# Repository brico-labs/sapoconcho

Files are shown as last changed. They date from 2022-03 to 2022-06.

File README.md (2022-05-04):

# [sapoconcho.bricolabs.cc](http://sapoconcho.bricolabs.cc)

Sapoconcho es un robot open-source educativo con que que introducirse en el mundo de la robótica y la programación. 
 
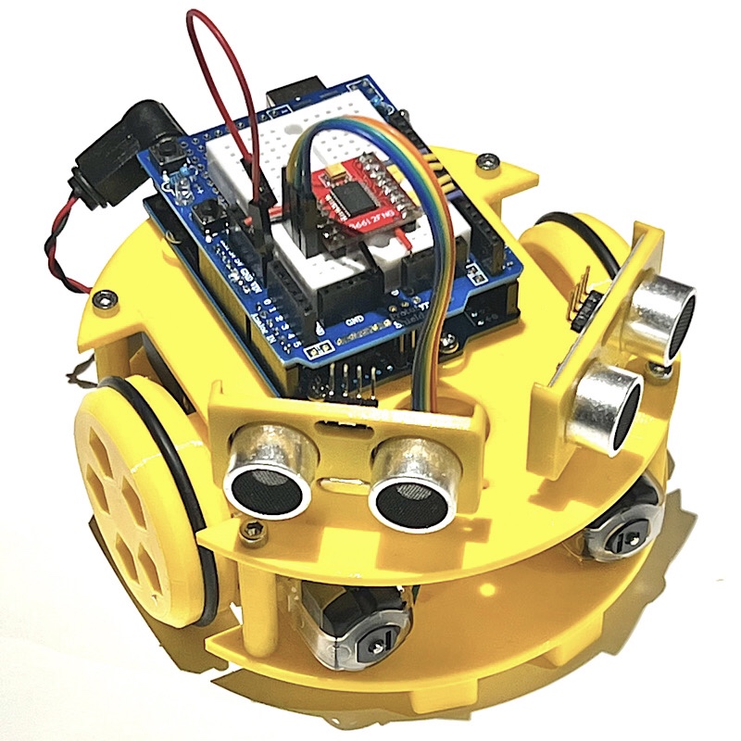
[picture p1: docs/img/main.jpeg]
Sapoconcho


Está ideado con el objetivo de ser lo más accesible posible:
- Componentes comunes, fáciles de encontrar y económicos.
- Diseño sencillo para imprimir y montar.
- Modular y extensible.

En este repositorio encontrarás:
- `3d_models` Los modelos 3D necesarios para crear un kit.
- `arduino` Ejemplos de código de programación del robot.
- `docs` Fuentes de la documentación que genera el sitio [sapoconcho.bricolabs.cc](https://sapoconcho.bricolabs.cc)

Revisa nuestro [CONTRIBUTING.md](CONTRIBUTING.md) si quieres modificar este repositorio o el sitio web.

Este proyecto antes estaba alojado en: 

- https://bricolabs.cc/wiki/proyectos/montaje_sapoconcho_xl
- https://bricolabs.cc/wiki/proyectos/sapoconcho
- https://github.com/felixstdp/sapoconcho

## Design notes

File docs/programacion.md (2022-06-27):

# Programación de Sapoconcho

Ahora que ya tienes tu Sapoconcho montado.. ¡vamos a programarlo!

Lo primero que necesitas es [Arduino IDE](https://www.arduino.cc/en/software), el programa que te permitirá escribir el código en el robot. Una vez instalado conecta el Arduino al ordenador usando el cable USB de tu kit y abre Arduino IDE.

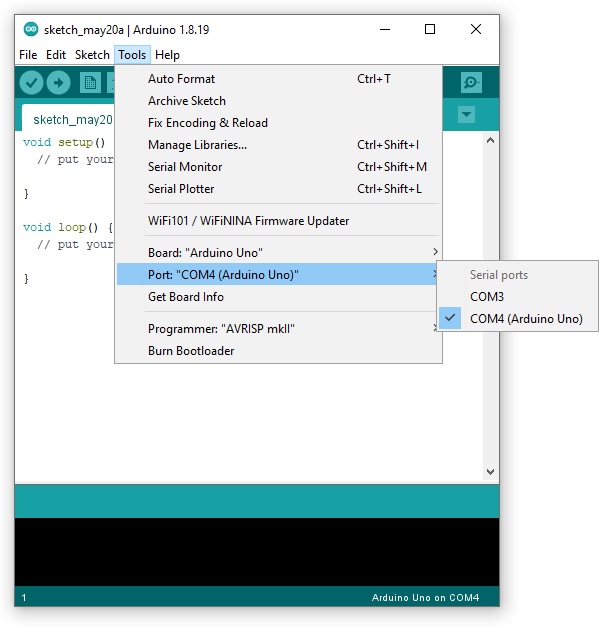
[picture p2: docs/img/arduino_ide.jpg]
Arduino IDE


En el menú *tools* selecciona:

- Board: Arduino Uno
- Puerto: el puerto USB en el que tienes conectado el Arduino.

## Programando en Arduino
Programar en Arduino es muy sencillo, tenemos dos funciones en las que escribir nuestro código:

- Setup: el robot hará lo que escribas aquí cuando se encienda.
- Loop: el robot hará esto continuamente una vez finalice el setup.

```c
void setup() {

}

void loop(){

}
```

!!! Note "Truco"

    Lo que escribas después de una doble barra "//" no se ejecutará, puedes usarlo para poner anotaciones en el código.

## Función de movimiento
Para decirle al robot que se mueva vamos a usar una función *drive* que os damos a continuación (copia y pégala al final de tu código):

```c
// Drive permite manejar los motores
// Izquierda y derecha admite valores de -100 a 100
// Tiempo en milisegundos
void drive(int izquierda, int derecha, int tiempo) 
{
  //Arduino UNO y driver TB6612/DRV8833
  const int AIN2 = 9; // PWMA
  const int AIN1 = 8;
  const int BIN1 = 7;
  const int BIN2 = 6; // PWMB

  pinMode(AIN1,OUTPUT);
  pinMode(AIN2,OUTPUT);
  pinMode(BIN1,OUTPUT);
  pinMode(BIN2,OUTPUT);

  izquierda=map(constrain(izquierda,-100,100),-100,100,-255,255);
  derecha=map(constrain(derecha,-100,100),-100,100,-255,255);

  digitalWrite(AIN1, izquierda<0);
  analogWrite(AIN2, izquierda + 255 * (izquierda < 0));
  digitalWrite(BIN1, derecha < 0);
  analogWrite(BIN2, derecha + 255 * (derecha < 0));

  delay(tiempo);
}
```

Esta función nos permite decirle al robot la velocidad de la rueda izquierda, rueda derecha y un tiempo. La velocidad de cada rueda admite valores de -100 a 100. El tiempo debemos indicarlo en milisegundos (1 segundo son 1000).

Ahora debemos llamar a esta función, para ello copia y pegar la siguiente linea dentro del *loop* de tu programa:
```c
drive(50,50,1000);
```

Para enviar el código al robot debes pulsar el botón *upload* upload.

Verás una barra de progreso y en unos pocos segundos ¡tu robot habrá recibido su primer código!

Ahora desconecta el cable USB del Sapoconcho, ponle la alimentación de las pilas y comprueba que avanza hacia delante.

??? Note "¿Sapoconcho avanza en linea recta?"

    Probablemente no.. esto se debe a que no existen dos motores exactamente iguales en el mundo y aunque les ordenemos ir a la misma velocidad no podrán. Intenta ajustar los valores *izquierda* y *derecha* para que tu sapoconcho avance recto.

**Movimientos de prueba**

Habrás notado que aunque le hemos puesto que avance un segundo Sapoconcho no para. Prueba a introducir una segunda instrucción a continuación de la anterior para indicar a sapoconcho que pare:

```c
drive(0,0,1000);
```

Si le envías este programa a Sapoconcho ahora verás que camina y para continuamente, ¡Esta es la mágia de la función *loop*! 

??? note "¿Se te ocurre como hacer que pare definitivamente?"

    ¡Exacto! En lugar de poner el código en el *loop* muévelo al *setup*, de esta forma sólo seguirá tus instrucciones una vez.

Ahora puedes probar a jugar con las distintas opciones que nos da la función *drive* y encadenarlas para conseguir una secuencia de movimientos:

- Movimiento hacia adelante: izquierda y derecha con valores positivos.
- Movimiento hacia atrás: izquierda y derecha con valores negativos.
- Giro en redondo: izquierda positivo, derecha negativo o viceversa.
- Giro en avance: valor de una rueda mayor que el de la otra.
- Parar: valores de izquierda y derecha en 0.

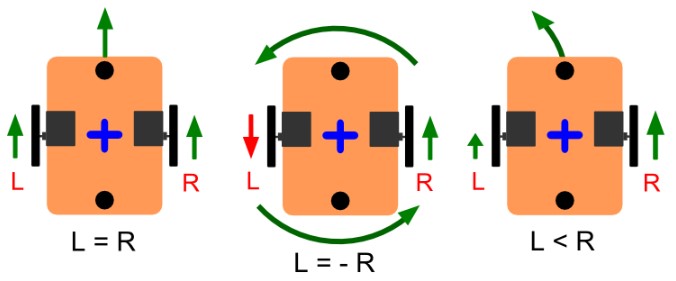
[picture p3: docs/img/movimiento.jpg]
Movimiento


??? note "¿Eres capaz de hacer un giro de 90 grados?"

    Para hacerlo deberás ajustar el tiempo que el robot está girando en redondo.

    Si lo consigues, intenta hacer un giro de 180 grados.

??? note "Intenta que el robot dibuje la forma de un cuadrado."

    Deberás concatenar avances y giros en redondo hacia un lado. Al estar en un bucle infinito solo necesitas dos instrucciones para conseguirlo.

    Si lo consigues, prueba con otras formas geométricas.

??? note "¿Saponconcho podrá moverse como una serpiente?"

    Concatenando varios giros en avance puedes conseguir que Sapoconcho se mueva en eses.

    Prueba a ponerle obstáculos e intenta evitarlos serpenteando.

## Sensores de ultrasonidos

Los sensores del ultrasonidos permiten a Sapoconcho medir la distancia a los objetos que tiene delante.

!!! info inline end "Sensor de ultrasonidos"

    El sensor HC-SR04 tiene cuatro pines: alimentación (VCC), trigger, echo y masa (GND), Trigger y echo los hemos unido con una soldadura para ahorrarnos un cable, aunque tenemos que advertir que es posible que modelos de algunos fabricantes no permitan esto, y al hacerlo no funcionen. 

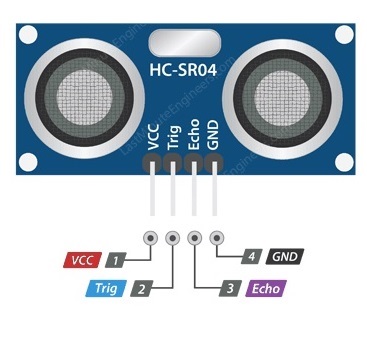
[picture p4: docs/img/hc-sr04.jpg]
hc-sr04


Los sensores tienen casi siempre dos pines de alimentación y uno o más pines de datos. La protoshield tiene en un lateral dos líneas para conectar la alimentación a positivo (5V) y negativo (GND).

Cablearemos con cables Dupont hembra-macho del sensor a la protoshield.

- VCC a uno de los conectores de 5V.
- GND a uno de los de masa.
- Trig o Echo al pin digital 2 del Arduino.

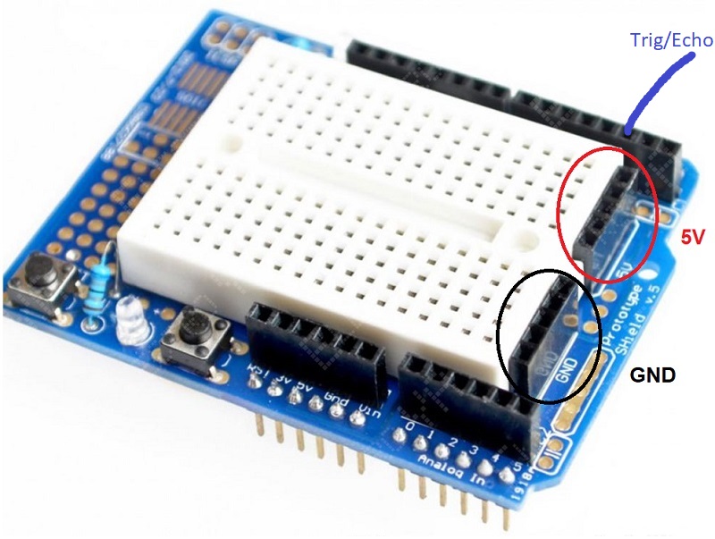
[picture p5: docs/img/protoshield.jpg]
Protoboard


El montaje del soporte a la placa superior es sencillo, con un tornillo M3x10 y una tuerca. La placa tiene tres orificios, usaremos el central para montar un único sensor o los laterales para montar dos.

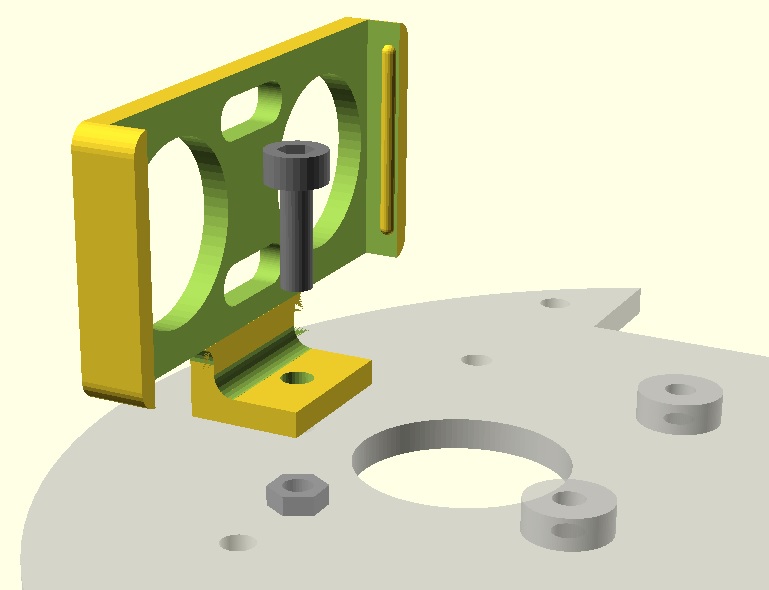
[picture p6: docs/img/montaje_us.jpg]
Montaje ultrasonidos


Para leer la distancia que mide el sensor usaremos una nueva función, que de nuevo copiaremos y pegaremos al final de nuestro programa.

```c
unsigned long sonar(int pin)
{
  double calibracion = 0.017; // Calibración del sensor
  pinMode(pin, OUTPUT);
  digitalWrite(pin,LOW); // Envía un pulso ultrasónico
  delayMicroseconds(5);
  digitalWrite(pin, HIGH);
  delayMicroseconds(10);
  pinMode(pin, INPUT);
  unsigned long tiempo=pulseIn(pin, HIGH); // Espera a recibir la respuesta
  unsigned long distancia= int(calibracion*tiempo); // Calcula la distancia
  return distancia;
}
```

Para usarla debemos llamarla pasándole el pin al que hemos conectado el sensor, en este caso el 2. Esta función nos devuelve un valor que guardaremos en una variable *distancia*.

```c
long int distancia = sonar(2);
```

El siguiente código permite leer el sensor y mostrar el resultado en el ordenador para poder comprobar que funciona y calibrarlo. Sapoconcho nos enviará los datos a través del cable USB.

??? Código
    ```c
    void setup()
    {
      Serial.begin(9600);
    }

    void loop()
    {
      unsigned long distancia = sonar(2); // invocamos a función de medir distancia
      Serial.print("Distancia: "); // Enviamos los valores a la consola
      Serial.print(distancia);
      Serial.println(" cm");
    }

    unsigned long sonar(int pin)
    {
      double calibracion = 0.017; // Calibración del sensor
      pinMode(pin, OUTPUT);
      digitalWrite(pin,LOW); // Envía un pulso ultrasónico
      delayMicroseconds(5);
      digitalWrite(pin, HIGH);
      delayMicroseconds(10);
      pinMode(pin, INPUT);
      unsigned long tiempo=pulseIn(pin, HIGH); // Espera a recibir la respuesta
      unsigned long distancia= int(calibracion*tiempo); // Calcula la distancia
      return distancia;
    }
    ```

En el ordenador deberemos abrir el monitor serial que está en la barra superior en el margen derecho serial.

!!! Note ""

    Al igual que con los motores, cada sensor es diferente y tendremos que calibrar el nuestro para que mida correctamente los centímetros. Puedes probar a ajustar la variable calibracion dentro de la función sonar para que los valores que te muestra sean más realistas.

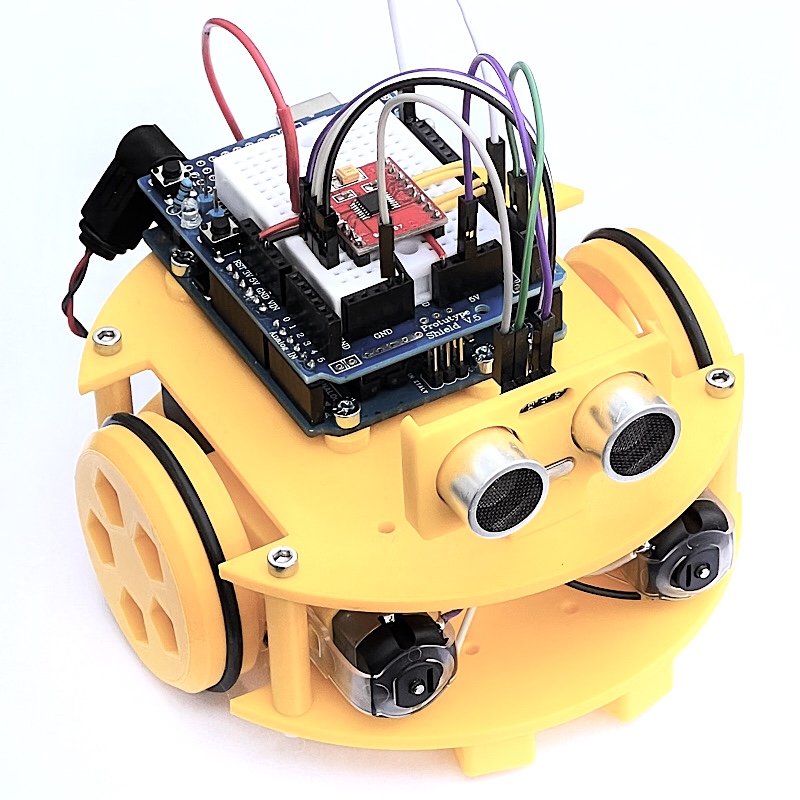
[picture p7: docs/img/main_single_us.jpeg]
Sapoconcho 1 us


**Mantener la distancia** 

Para utilizar el sensor combinado con el movimiento en Sapoconcho necesitaremos utilizar la instrucción *if - else*. En el siguiente programa comprobamos la distancia, si el obstáculo está lejos le decimos al robot que avance, si está cerca que retroceda.

??? Código
    ```c
    void setup() {

    }

    void loop() {
      long int distancia = sonar(2);
      if (distancia<10){
        drive(-75,-75,50);
      }
      else {
        drive(75,75,50);
      }
    }

    void drive(int izquierda, int derecha, int tiempo) 
    {
      //Arduino UNO y driver TB6612/DRV8833
      const int AIN2 = 9; // PWMA
      const int AIN1 = 8;
      const int BIN1 = 7;
      const int BIN2 = 6; // PWMB

      pinMode(AIN1,OUTPUT);
      pinMode(AIN2,OUTPUT);
      pinMode(BIN1,OUTPUT);
      pinMode(BIN2,OUTPUT);

      izquierda=map(constrain(izquierda,-100,100),-100,100,-255,255);
      derecha=map(constrain(derecha,-100,100),-100,100,-255,255);

      digitalWrite(AIN1, izquierda<0);
      analogWrite(AIN2, izquierda + 255 * (izquierda < 0));
      digitalWrite(BIN1, derecha < 0);
      analogWrite(BIN2, derecha + 255 * (derecha < 0));

      delay(tiempo);
    }

    unsigned long sonar(int pin)
    {
      double calibracion = 0.017; // Calibración del sensor
      pinMode(pin, OUTPUT);
      digitalWrite(pin,LOW); // Envía un pulso ultrasónico
      delayMicroseconds(5);
      digitalWrite(pin, HIGH);
      delayMicroseconds(10);
      pinMode(pin, INPUT);
      unsigned long tiempo=pulseIn(pin, HIGH); // Espera a recibir la respuesta
      unsigned long distancia= int(calibracion*tiempo); // Calcula la distancia
      return distancia;
    }
    ```

Esto evitará que el robot choque con una pared hacia la que va de frente, ademássi en lugar de una pared ponemos la mano, conseguiremos manejar 'a distancia' nuestro robot.

!!! Note ""

    Como diversión si estamos trabajando en grupo podemos poner todos los robots en fila y encenderlos a la vez a ver qué pasa.

**Evitar obstáculos**  

Si a nuestro robot le ponemos dos sensores de distancia podemos ver por donde está el obstáculo más cercano y girar hacia el lado contrario evitándolo.

??? Código
    ```c
    void setup() {
    }

    void loop() {
      long int izquierda = sonar(2);
      long int derecha = sonar(3);
      long int distancia = min(izquierda, derecha);
      if (distancia<10){
        if (izquierda<derecha){
          drive(75,-75,100);
        }
        else{
          drive(-75,75,100);
        }
      }
      else{
        drive(75,75,50);
      }
    }

    void drive(int izquierda, int derecha, int tiempo) 
    {
      //Arduino UNO y driver TB6612/DRV8833
      const int AIN2 = 9; // PWMA
      const int AIN1 = 8;
      const int BIN1 = 7;
      const int BIN2 = 6; // PWMB

      pinMode(AIN1,OUTPUT);
      pinMode(AIN2,OUTPUT);
      pinMode(BIN1,OUTPUT);
      pinMode(BIN2,OUTPUT);

      izquierda=map(constrain(izquierda,-100,100),-100,100,-255,255);
      derecha=map(constrain(derecha,-100,100),-100,100,-255,255);

      digitalWrite(AIN1, izquierda<0);
      analogWrite(AIN2, izquierda + 255 * (izquierda < 0));
      digitalWrite(BIN1, derecha < 0);
      analogWrite(BIN2, derecha + 255 * (derecha < 0));

      delay(tiempo);
    }

    unsigned long sonar(int pin)
    {
      double calibracion = 0.017; // Calibración del sensor
      pinMode(pin, OUTPUT);
      digitalWrite(pin,LOW); // Envía un pulso ultrasónico
      delayMicroseconds(5);
      digitalWrite(pin, HIGH);
      delayMicroseconds(10);
      pinMode(pin, INPUT);
      unsigned long tiempo=pulseIn(pin, HIGH); // Espera a recibir la respuesta
      unsigned long distancia= int(calibracion*tiempo); // Calcula la distancia
      return distancia;
    }
    ```

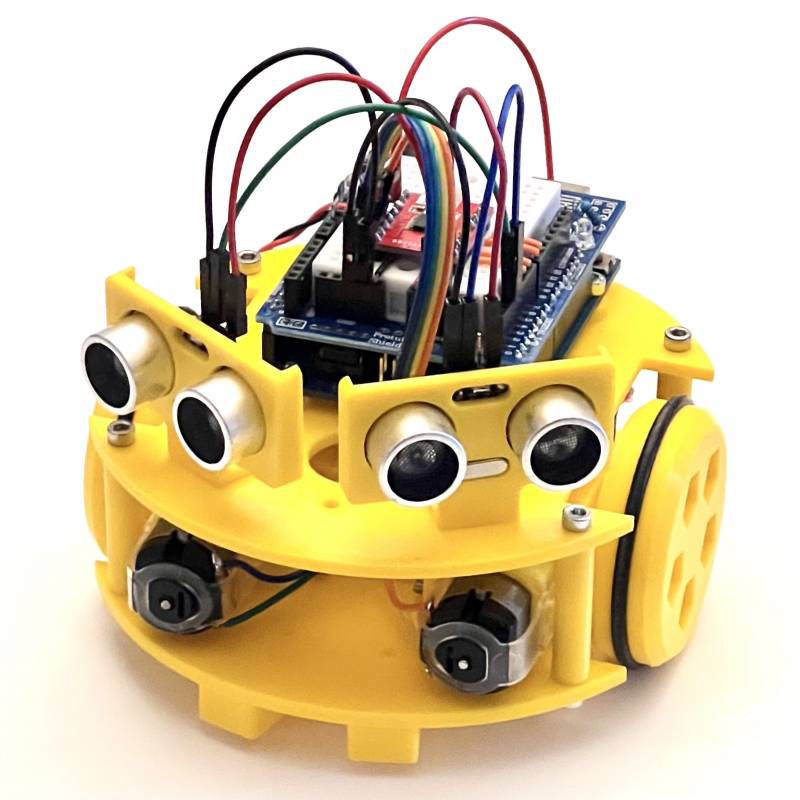
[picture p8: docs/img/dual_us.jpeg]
Sapoconcho 2 us


!!! Note ""

    Esto también es posible hacerlo con un solo sensor, pero tendrás que parar el robot y girarlo para medir en que dirección está el terreno más despejado ¿Eres capaz de hacerlo?

## Sensores de líneas

Los sensores infrarrojos de líneas, tanto con salida analógica como digital utilizan tres pines: alimentación (VCC), masa (GND) y señal. Debes revisar tu sensor, según el fabricante los sensores podrían estar en otro orden, no tiene por qué coincidir con la foto.

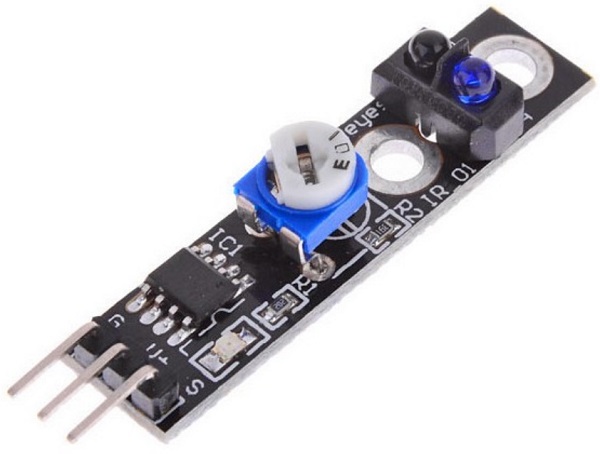
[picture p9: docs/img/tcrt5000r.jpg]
tcrt5000r


Utilizaremos sensores basados en reflexión TCRT5000 con regulador (importante) que se montarán en el chasis inferior y se cablean a 5v, GND y dos entradas analógicas entre A0 y A5 (con cables Dupont H-M de 20cm).

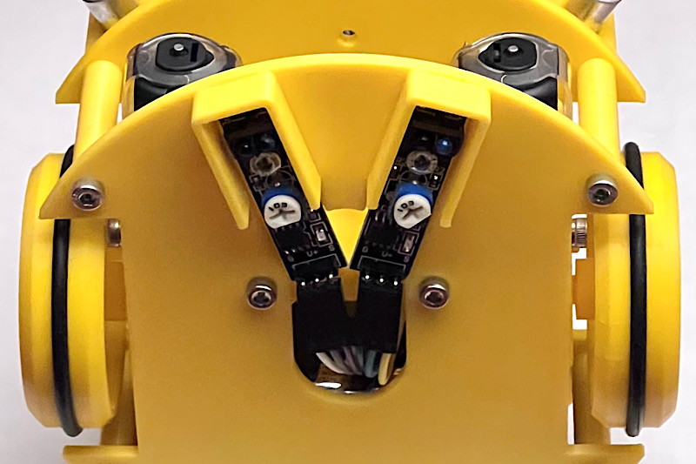
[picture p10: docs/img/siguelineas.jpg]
Siguelineas


**Seguir una línea**

Para leer los sensores no necesitamos una función extra, Arduino puede hacerlo con su propia función analogRead(pin). El siguiente código lee los dos sensores y si uno de ellos está sobre la línea negra gira hacia el otro lado para evitarla (necesita la función drive).

```c
void setup() {
}

void loop()
{
  if (analogRead(A0)<500){
    drive(-75,75,100);
  }
  if (analogRead(A1)<500) {
    drive(75,-75,100);
  } 
  drive(75,75,100);
}
```

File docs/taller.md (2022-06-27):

# Preparar un taller de Sapoconcho

Sapoconcho fue concebido principalmente para impartir talleres de robótica. El público principal para el que está pensado es para niños de entre 11 y 18 años o formadores que posteriormente utilizarán Sapoconcho en sus clases. Es muy habitual y recomendable que si los niños son pequeños (11-14 años) hagan el taller acompañados por un adulto.

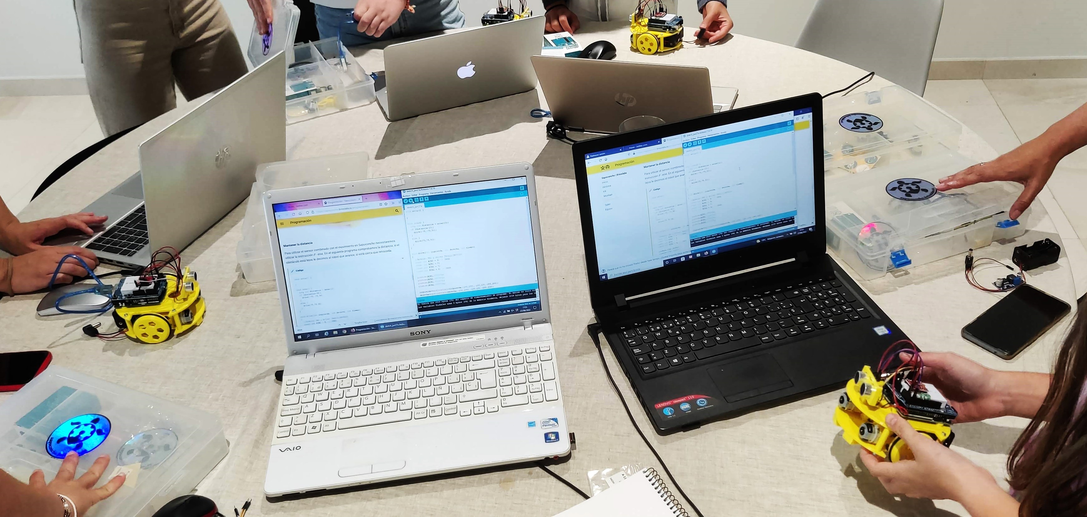
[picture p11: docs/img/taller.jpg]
taller


## Duración del taller
Basándonos en experiencias anteriores podemos indicar las siguientes duraciones:

- Montaje: 60 minutos
- Programación movimiento: 45 minutos
- Programación ultrasonidos: 45 minutos
- Programación siguelineas: 45 minutos

Es posible alargar el taller o dividirlo en dos sesiones si se incluye la parte de preparado de los kits. Para esta parte la edad recomendada debería ser un poco mayor ya que requiere soldar con estañador.

## Preparativos previos

### Preparando los kits

Las siguientes indicaciones pueden ahorrarnos problemas durante el taller:

- Preparar al menos un 1 kit extra por cada 10 por si faltan o fallan piezas en alguno.
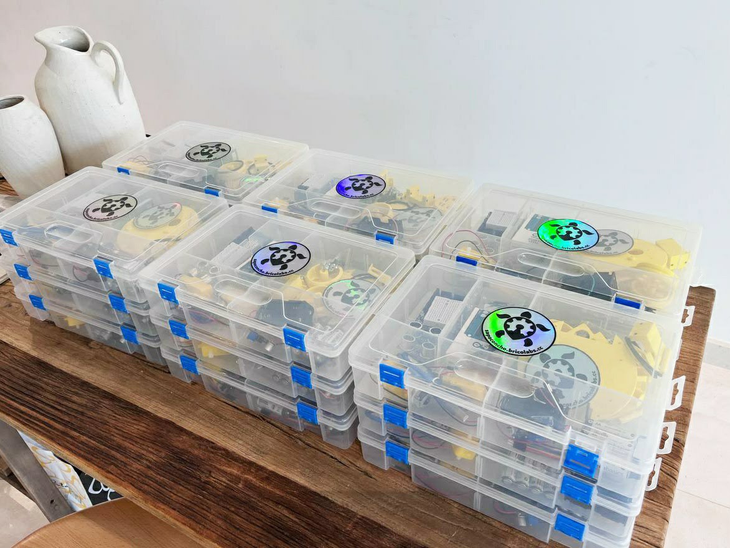
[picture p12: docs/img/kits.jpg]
kits

- Revisar los diámetros de los agujeros en las piezas impresas, especialmente los del eje de los motores que deben entrar justos.
- Soldar los pines del driver de motores.
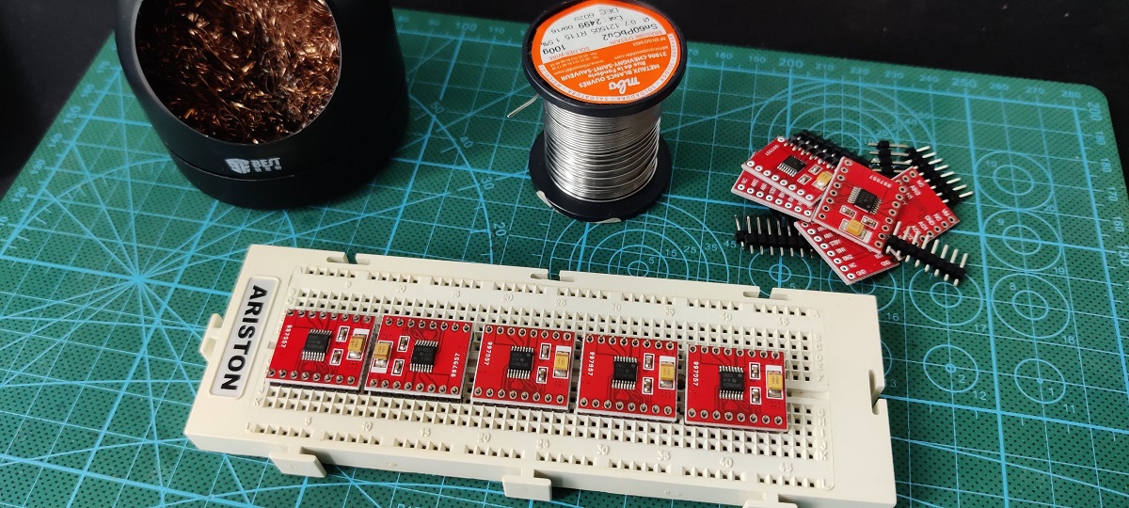
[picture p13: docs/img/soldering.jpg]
soldering

- Cortar y pelar los cables para breadboard a medida.
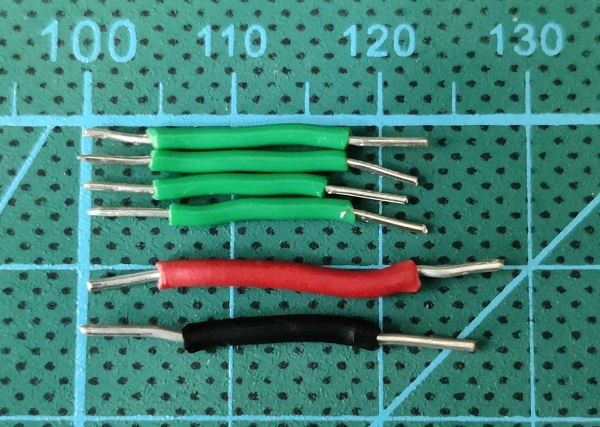
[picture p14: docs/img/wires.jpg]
wires

- Soldar cables al step-up y al conector de alimentación.
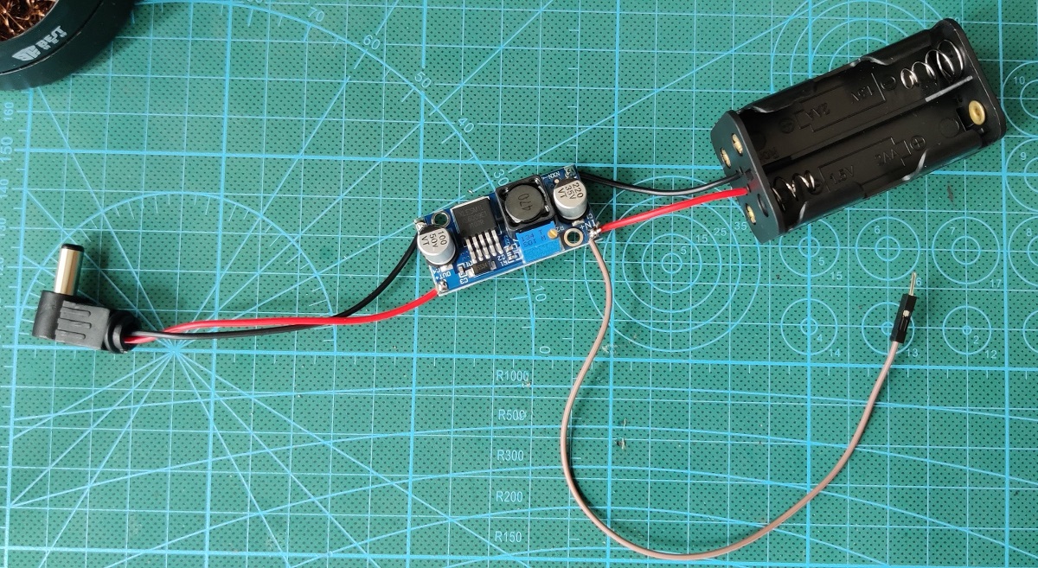
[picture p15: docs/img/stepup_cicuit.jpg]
stepup_cicuit

- Regular el voltaje del step-up.
- Soldar los dos pines centrales del sensor de ultrasonidos.

### Preparativos de los participantes
Es recomendable que los participantes traigan Arduino IDE instalado en sus portátiles de forma que evitemos problemas con la descarga o instalación durante el taller.

## Durante el taller

Es recomendable tener a mano los siguientes materiales y herramientas por si fuesen necesarias:  

- Estación de soldadura (estañador, estaño y demás útiles)
- Destornillador eléctrico con punta hexagonal
- Cable para breadboard
- Alicates de corte
- Pelacables
- Multímetro
- Lima y broca de 3mm (por si los diámetros del eje de las ruedas fuesen pequeños)
- Loctite (por si los diámetros del eje de las ruedas son demasiado holgados)
- Cinta de doble cara
- Bridas
- Instalador de Arduino IDE en un pen-drive

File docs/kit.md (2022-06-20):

# Un Kit Sapoconcho

Un kit de Sapoconcho es un paquete con todas las piezas necesarias para montar un Sapoconcho. Para hacerte uno necesitarás una serie de materiales que detallaremos a continuación:

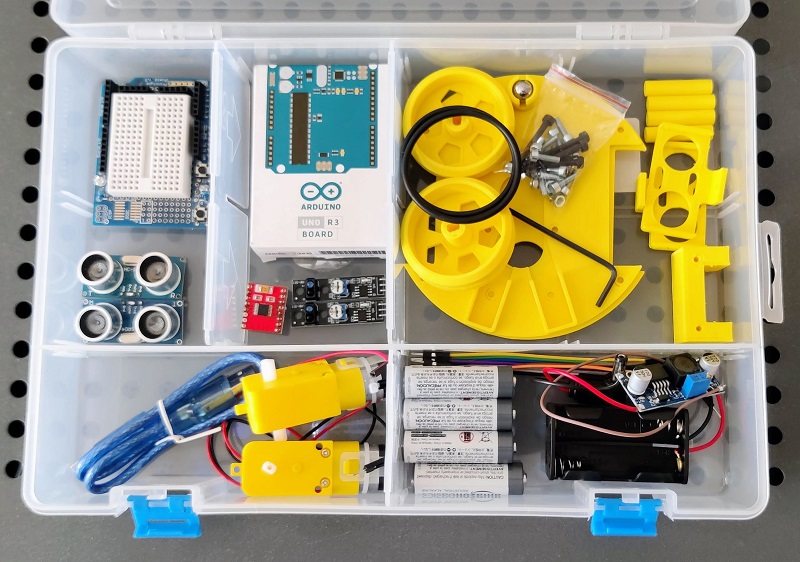
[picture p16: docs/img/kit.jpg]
kit


## Piezas imprimibles
El chasis de Sapoconcho consta de las siguientes piezas:

- Bases superior e inferior.
- Soporte de motores (1 unidad).
- Pilares de unión (o separación) de las dos bases (4 unidades). Pueden usarse en su lugar separadores de circuitos de 30mm.
- Ruedas (2 unidades).
- Soporte de sensores de ultrasonidos (1 ó 2 unidades).

En una impresora típica de 200x200mm se pueden imprimir todas las piezas en dos tandas.

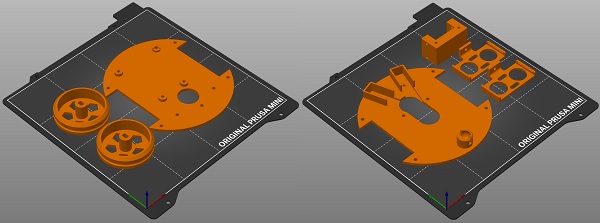
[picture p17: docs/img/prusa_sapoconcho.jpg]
Impresion3D


Todas las piezas están en [este repositorio de Github](https://github.com/brico-labs/sapoconcho/tree/main/3d_models). Ahí puedes encontrar los archivos originales de OpenSCAD para modificarlos a tu gusto o los STL para imprimir directamente.

## Listado de materiales (BOM)

- Arduino UNO o compatible.
- Protoshield para Arduino UNO.
- Driver de motores TB6612 o DRV8833.
- Dos motores amarillos. Sabemos que es un término muy genérico, pero si estás metido un poco en el mundo maker/DIY o haces una búsqueda rápida en tu plataforma favorita verás a qué nos referimos. Es un tipo de motor de corriente continua muy usado en todo tipo de proyectos y kits, muy fácil de conseguir y muy económico. No necesitamos las ruedas que traen a veces.
- Gomas de fontanería para las ruedas (2ud). Medida 45×3 mm.
- Bola de acero de 10 mm.
- Sensores ultrasónicos HC-SR04 (1 ó 2 ud).
- Sensores de líneas por infrarrojos (2 ud).
- Portapilas para montar 4 pilas AA (dos encima y dos debajo).
- Elevador de tensión DC-DC (step-up, con los integrados LM2587/XL6009).
- Clavija de alimentación para Arduino UNO (5.5×2.1 mm).
- Tornillos M3 (12 ud M3x10, 4 ud M3x30, 4d M3x6).
- Tuercas M3 (4 ud).
- Cables Dupont M-H de 20mm y de 10mm.
- Cable USB-A a USB-B
- Cables de tres colores (rojo, negro y otro) para breadboard.

Por si os es de utilidad, os dejamos una [lista de la compra en Amazon](https://www.amazon.es/hz/wishlist/ls/9FKST3X6WCM?viewType=list).

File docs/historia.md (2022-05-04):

# Historia

!!! Note ""

    Yet Another Training Robot.

## El origen

Sabemos que lo que hacemos no es ninguna novedad. Este tipo de robots se puede encontrar en modelos comerciales y en muchos tutoriales a lo largo y ancho de la web. Sin embargo tenemos una experiencia de varios años en [Bricolabs](http://bricolabs.cc) que no queremos que se pierda. Llevamos tiempo cocinando la idea de crear un proyecto paralelo en forma a [Escornabot](https://escornabot.com/) para el siguiente segmento de edad, aunque por supuesto esto no es excluyente.

- A lo largo del año 2013 participamos en la iniciativa [KiiCS](https://kiicsmc2.wordpress.com/2013/10/10/nuevos-talleres-kiics/) de los Museos Científicos de A Coruña que se desarrolló en nuestra casa de acogida, la Domus. En estos talleres se utilizaron unos kits comerciales y que tienen algunas limitaciones además de su precio. Los destinatarios en aquella ocasión eran adolescentes y después se extendió a profesores de tecnología, que se han mantenido en otros posteriores. Además de diseñar y probar los cursos se crearon librerías de Arduino para el control de los motores con instrucciones sencillas. Una buena experiencia que nos sirvió para ver qué cosas funcionan bien en un curso y resultan entretenidas y divertidas.

- Casi al mismo tiempo fue surgiendo el proyecto [Escornabot](https://escornabot.com/) y el buen funcionamiento de éste nos anima a buscar un proyecto complementario dirigido a un segmento de edad mayor y a intentar otros objetivos: programar los robots con código fuente. Empezar editando los programas que ya existen, y poco a poco animarse a crear otras funciones y -por qué no- añadir otros módulos electrónicos.

- Además en los últimos años varios miembros de Bricolabs hemos hecho nuestros propios robots 'tortuga' con muchas funciones diferentes. También hemos seguido experimentando con diferentes plataformas de hardware y diferentes lenguajes de programación.

La idea es poner orden en toda la documentación que ya existe y que fue apareciendo por nuestra [wiki](http://bricolabs.cc/wiki). De ese modo se pretende poner en un único sitio toda la información necesaria para hacer dos cosas:

- Construir tu propio robot paso a paso, programarlo y usarlo como base para aprender o construir lo que quieras.

- Un curso completo autocontenido para que cualquiera puede ofrecerlo, modificarlo y extender la cadena del conocimiento hasta el infinito y más allá.

## Los primeros prototipos

| Prototipo | |
| --- | --- |
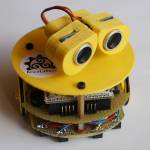
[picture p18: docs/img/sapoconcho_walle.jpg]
sapoconcho_walle
| Wall.E |  |
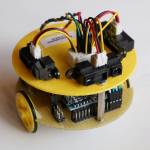
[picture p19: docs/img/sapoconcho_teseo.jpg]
sapoconcho_teseo
| Teseo |  |
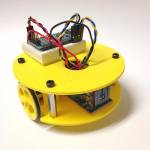
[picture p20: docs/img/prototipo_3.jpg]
prototipo_3
| KIS |  |
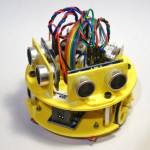
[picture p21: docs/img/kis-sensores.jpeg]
kis-sensores
| KIS con sensores |  |

## Sapoconcho original de 90mm
Este fue el primer diseño con piezas impresas ( aunque hubo una fase anterior recortando protoboards). Fue un diseño que se ajustó a 90mm de diámetro pensando en que pudiese entrar en el concurso de laberinto de la [OSHWDEM](https://oshwdem.org/).

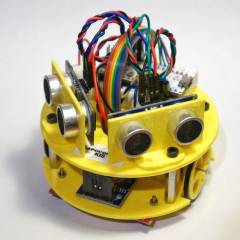
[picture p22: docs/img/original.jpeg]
original


Sólo se necesitaban separadores de circuitos de 25mm (4 ud) y tornillos M2.5×20 para montar los motores al chasis inferior con sus soportes.

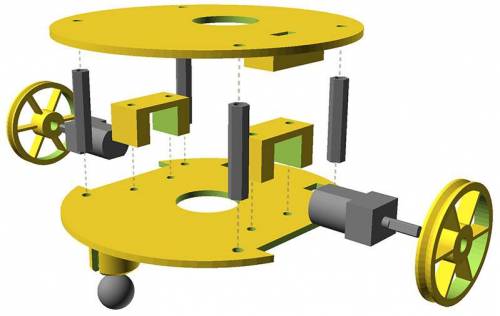
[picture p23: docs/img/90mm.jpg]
90mm


Los pasos para montarlo eran los siguientes:

1.  Monta la bola y los motores en la base inferior. La primera entra a presión, los motores con sus soportes atornillados (M2.5×20 tuerca) .
2.  Pega la controladora de motores y el portapilas a la base inferior con cinta adhesiva de doble cara.
3.  Monta la base superior con los separadores de circuitos.
4.  Pega la breadboard en la base superior para el Arduino micro. En su lugar puedes usar un Arduino UNO, que también cabe.
5. (opcional). Monta los soportes para los sensores SR-04 sobre la base superior.

Conecta la placa de motores al Arduino con el esquema siguiente.

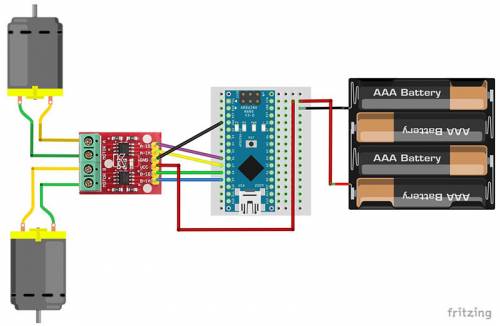
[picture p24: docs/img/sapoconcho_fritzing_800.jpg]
sapoconcho_fritzing_800


## Sapoconcho 2021. The Expanse
Los modelos iniciales del proyecto utilizaban micromotores de tipo N20 en un chasis de 90mm de diámetro. Aunque sigue siendo un diseño válido, en 2021 hemos creado un nuevo chasis un poco más grande para poder expandir el ecosistema.

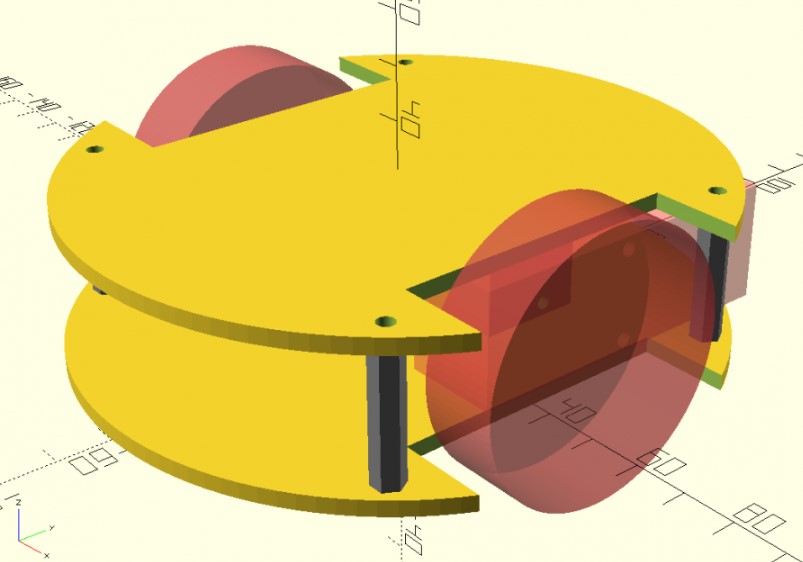
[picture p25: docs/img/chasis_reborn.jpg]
Chasis reborn


El nuevo chasis utiliza motores amarillos y tiene 120mm de diámetro, manteniendo el formato tortuga. Sabemos que 'motor amarillo' es un término muy genérico, pero si estás metido un poco en el mundo maker/DIY o haces una búsqueda rápida en tu plataforma favorita verás a qué nos referimos. Es un tipo de motor de corriente continua muy usado en todo tipo de proyectos y kits, muy fácil de conseguir y muy económico. Esos motores suelen traer una rueda pero no es necesario que la compres, utilizaremos una impresa de menor tamaño con una goma para que agarre. Además de los nuevos motores, el nuevo tamaño permite utilizar un pack de 4 pilas AA (y añadirle un módulo step-up si es necesario) o una batería recargable 18650.

Cuando tengan motores Epstein en Aliexpress habrá que reestudiar el proyecto.

Esto nos va a permitir aumentar la versatilidad del proyecto al poder meter más elementos en el chasis, y ampliar el número de plataformas hardware disponibles.

## Sapoconcho mClon
Cuando pensamos en ampliar el ecosistema inmediatamente se nos ocurrió que sería un desperdicio no aprovechar el trabajo estupendo del proyecto [mClon](https://tecnoloxia.org/mclon/) de [A Industriosa](https://aindustriosa.org/). Como el mClon utiliza dos motores amarillos, sensores de líneas y de ultrasonidos, la compatibilidad es total. En realidad lo único que hemos hecho es un chasis en el que se pueden montar los mismos elementos, tanto en la versión ShieldClon como en la versión ProtoShield. Os mostramos sólo las fotos del resultado. El proyecto está fantásticamente documentado en su web. Necesitarás usar una versión especial de la placa superior que tiene ya los soportes para un Arduino UNO (upper_plate_UNO_v1 ó v2). También una versión especial de la placa inferior que tiene unos soporte con parasol para los sensores de infrarrojos. Esa pieza es mejor que sea negra o cubrir esos parasoles con cinta o pintura negra.

Versión ProtoShield

mclon

Versión ShieldClon

sc_mclon_v2

Para poder utilizar el portapilas 4xAA (con step-up) es necesario hacer unos pequeños hacks a la placa de XDeSIG. Además de no montar el conector USB, hay que cambiar la resistencia de 2.2 ohm por una de 0 ohm (sí, has leído bien, cero, aunque puedes también hacer un puente con un cable), y en lugar del step-up para cargar la batería colocar un regulador LM7805.

lm7805

## Versiones procrastinadas

- Sapoconcho Pico: el nuevo microcontrolador de Raspberry y una controladora de motores nos permitirá iniciarnos en el mundo de MicroPython.
- Sapoconcho micro:bit: la renovada plataforma de BBC nos permitirá elegir entre programar con bloques tipo Scratch o Python.
- Sapoconcho Zero: para quien quiera Python a toda potencia con una Raspi Zero y diferentes HATs.
- Sapoconcho RC: instala la placa que recomendamos en el proyecto [MeccanoRC](https://bricolabs.cc/wiki/proyectos/meccano_rc) y tu chasis ya se mueve!

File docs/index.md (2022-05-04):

# Sapoconcho

!!! Note ""

    **sapoconcho**  
    **1.** f. (*galego*) O sapoconcho (*Emys orbicularis*) é unha tartaruga da familia Emydidae e única representante do xénero Emys, que se atopa no centro e sur de Europa, Asia occidental, Norteamérica e a zona mediterránea de África.

Sapoconcho es un robot open-source educativo con el que puedes introducirte en el mundo de la robótica y la programación. Es apropiado para niños de a partir de 11 años.
 
Sapoconcho

Está ideado con el objetivo de ser lo más accesible posible:

- Abierto y documentado.
- Componentes comunes, fáciles de encontrar y económicos.
- Diseño sencillo para imprimir y montar.
- Modular y extensible.

En este sitio encontrarás:

- Historia del proyecto
- Listado de materiales para crear un kit de Sapoconcho.
- Tutorial de montaje y programación de un Sapoconcho.
- Guia y materiales para preparar un taller de Sapoconcho.

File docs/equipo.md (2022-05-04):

# Equipo

Sapoconcho es un proyecto de la asociación [Bricolabs](http://bricolabs.cc).

Su creador y actual mantenedor del proyecto es:

- [Félix](https://github.com/felixstdp)

En el proyecto han colaborado:

- [Sergio](https://bricolabs.cc/wiki/user/salvari)
- [Manolo](https://bricolabs.cc/wiki/user/manolomira)
- Rafa
- [Dani](https://github.com/dalogax)

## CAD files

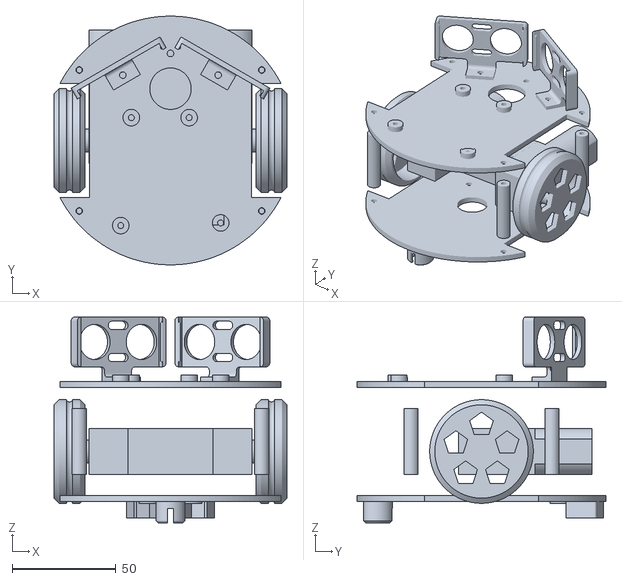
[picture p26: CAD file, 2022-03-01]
3d_models/stl/assembly.stl
112.4 x 120.0 x 99.3

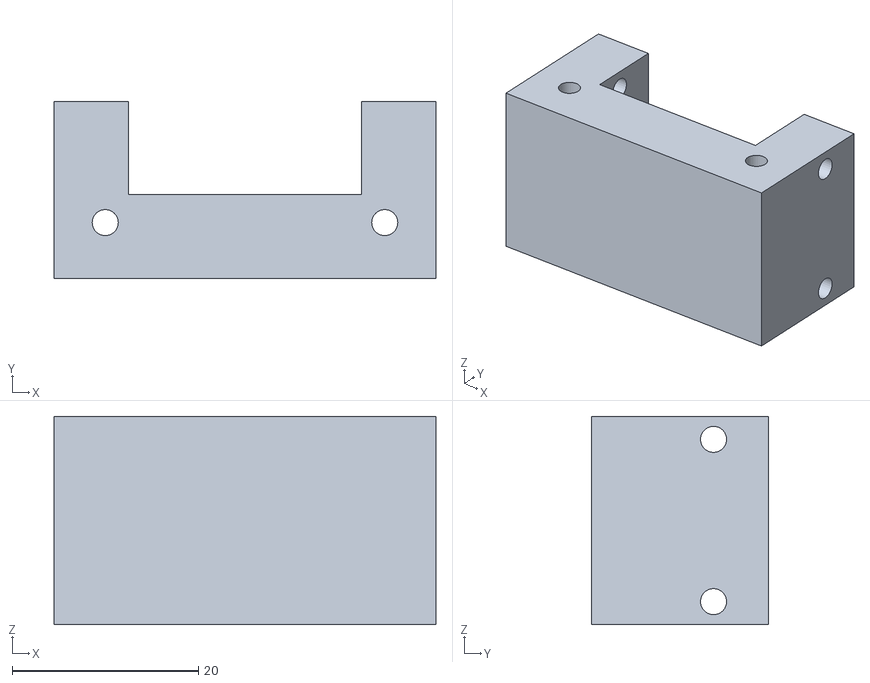
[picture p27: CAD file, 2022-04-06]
3d_models/scad/motor_support.stl
41.0 x 19.0 x 22.3

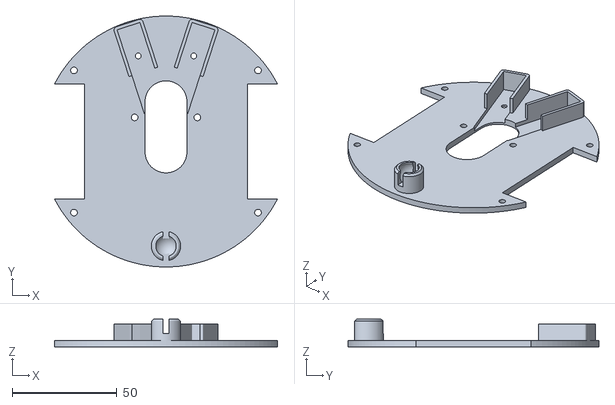
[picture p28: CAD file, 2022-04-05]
3d_models/stl/lower_plate.stl
106.6 x 120.0 x 13.3

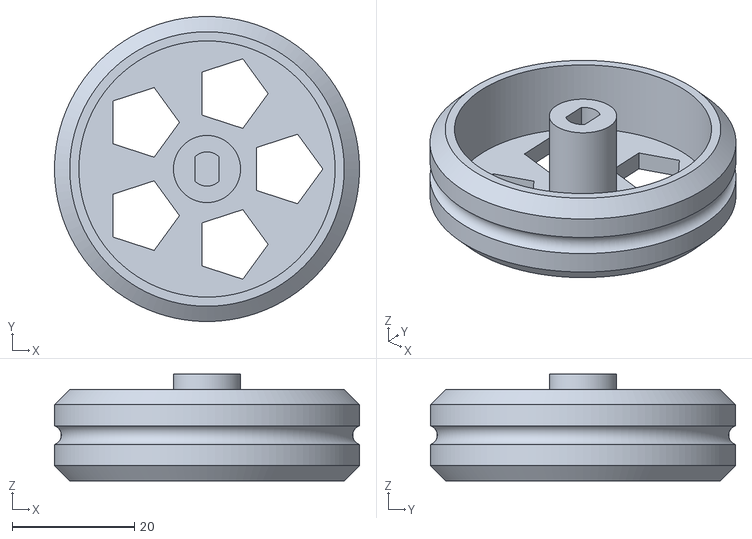
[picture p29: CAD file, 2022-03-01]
3d_models/stl/wheel.stl
50.0 x 50.0 x 17.5

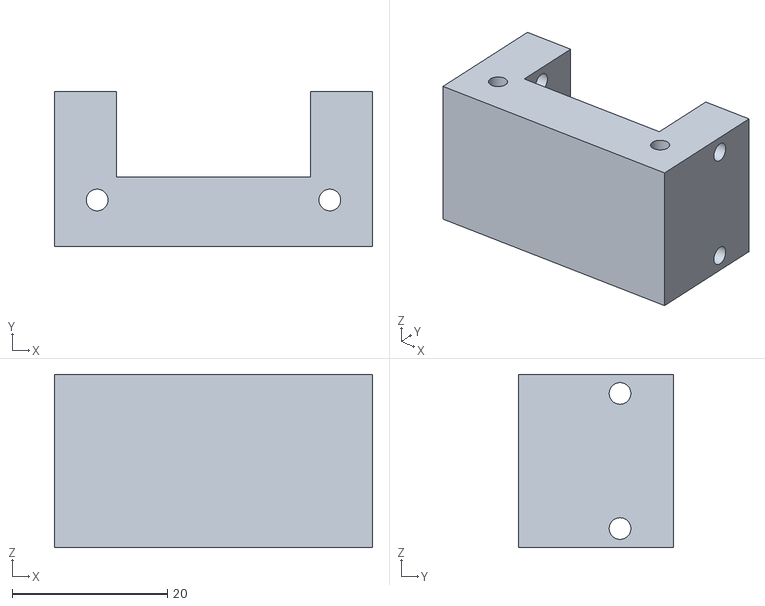
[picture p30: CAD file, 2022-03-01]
3d_models/stl/motor_support.stl
41.0 x 20.0 x 22.3

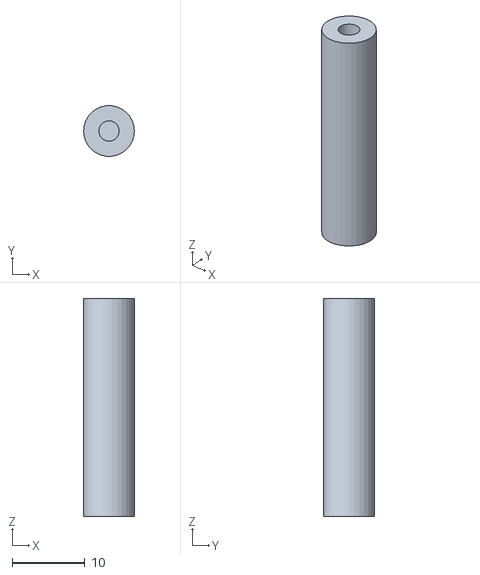
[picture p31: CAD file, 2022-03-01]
3d_models/stl/pillar.stl
7.00 x 6.96 x 30.0

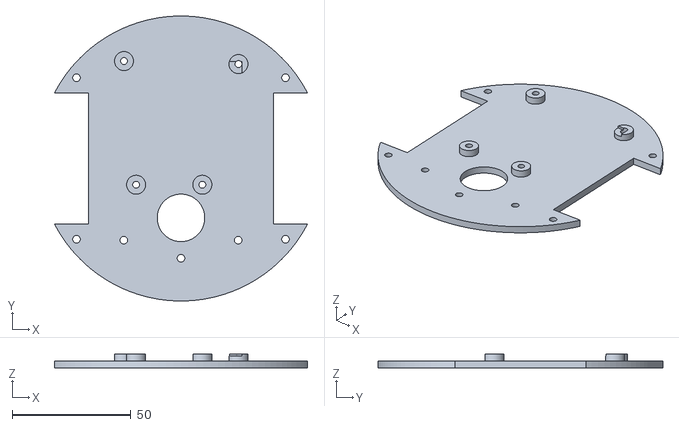
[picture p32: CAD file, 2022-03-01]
3d_models/stl/upper_plate.stl
106.6 x 120.0 x 6.00

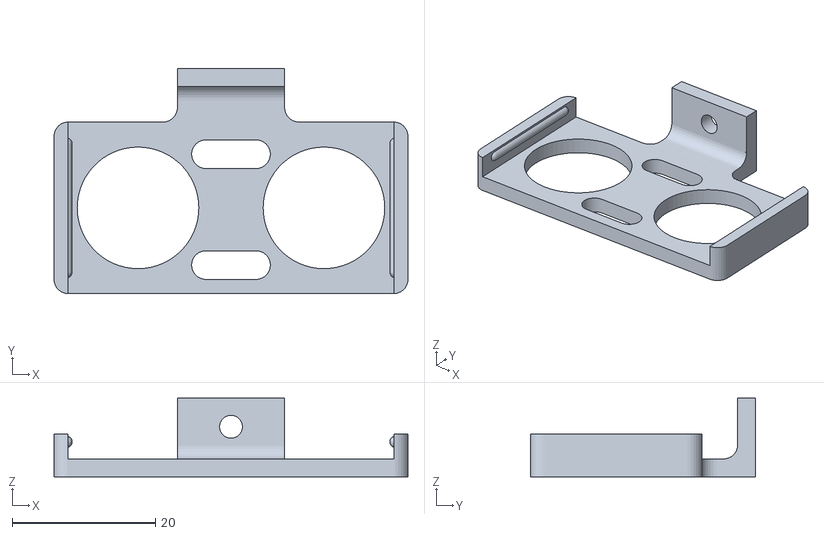
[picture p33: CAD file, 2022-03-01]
3d_models/stl/US_support.stl
49.5 x 31.5 x 11.0

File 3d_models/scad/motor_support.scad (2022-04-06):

$fn=30;

difference(){
translate([-20.5,6,0])cube([41,19,22.35]);
translate([-12.5,15,-10])cube([25,12,50]);
translate([0,19.1,2.465])rotate([0,90,0])
cylinder(d=2.8,h=50,center=true,$fn=30);
translate([0,19.1,19.885])rotate([0,90,0])
cylinder(d=2.8,h=50,center=true,$fn=30);
translate([15,12,0])cylinder(d=2.8,h=30);    
translate([-15,12,0])cylinder(d=2.8,h=30);    
}

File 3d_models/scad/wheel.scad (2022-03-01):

$fn=120;
difference(){
union(){
cylinder(h=2.5,d1=45,d2=50);
translate([0,0,2.5])cylinder(d=50,h=10);
translate([0,0,12.5])cylinder(h=2.5,d2=45,d1=50);
}
translate([0,0,7.5])
rotate_extrude(angle = 360, convexity = 2) {
translate([25.5,0,0])circle(1.6);
}
translate([0,0,3])cylinder(d=42,h=15);

for (i=[0:72:350]){
rotate([0,0,i])
translate([13,0,-1])cylinder(d=12,h=15,$fn=5);
}
}
difference(){
cylinder(d=11,h=17.5);
translate([0,0,9.05])
scale(1.05)    // ajustar según impresora
    intersection(){
cylinder(d=5.35,h=9);
translate([0,0,4])cube([3.7,6,9],center=true);
    }
}

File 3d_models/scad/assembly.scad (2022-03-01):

$fn=120;

translate([0,0,-7])scale([1,1,-1])lower_plate();
translate([0,0,45])scale([1,-1,1])upper_plate();
translate([0,-0.5,3])motor_support();
#translate([20.5,-11.2,3])motorandwheel();
#scale([-1,1,1])translate([20.5,-11.2,3])motorandwheel();
   
translate([44,34,3])pillar();    
translate([-44,34,3])pillar();    
translate([44,-34,3])pillar();    
translate([-44,-34,3])pillar();

#translate([25,35,67])rotate([0,0,150])
rotate([-90,0,0])us_support();
#translate([-25,35,67])rotate([0,0,210])
rotate([-90,0,0])us_support();

module lower_plate(){
$fn=120;
translate([0,-50,2.3])ballcaster();
rotate([0,0,15])translate([0,44,6.5])irshade();
rotate([0,0,-15])translate([0,44,6.5])irshade();
 
difference(){
cylinder(d=120,h=3);
translate([39,-27.5,-1])cube(55);
scale([-1,1,1])translate([39,-27.5,-1])cube(55);
translate([44,34,-1])cylinder(d=3.2,h=5);    
translate([-44,34,-1])cylinder(d=3.2,h=5);    
translate([44,-34,-1])cylinder(d=3.2,h=5);    
translate([-44,-34,-1])cylinder(d=3.2,h=5); 
translate([0,-5,0])cylinder(d=16,h=5);
translate([15,11.5,0])cylinder(d=3.2,h=30);    
translate([-15,11.5,0])cylinder(d=3.2,h=30); 
rotate([0,0,15])translate([0,39.5,0])cylinder(d=2.8,h=30); 
rotate([0,0,-15])translate([0,39.5,0])cylinder(d=2.8,h=30); 
}

module ballcaster(){
difference(){
union(){
cylinder(d=14,h=10);
translate([0,0,10])cylinder(r1=7, r2=6, h=1);
}
translate([0,0,7])cylinder(d=9.8,h=25);
translate([0,0,7.9])sphere(d=10.8);
translate([0,0,12])cube(size=[3,15,16],center=true);
}
}

module irshade(){
difference(){
minkowski(){
cube([10,28,9],center=true);
cylinder(d=3,h=0.001,$fn=12);
}
translate([0,-1,1])cube([10.25,30,9],center=true);
translate([0,-15,1])cube([15,30,9],center=true);
translate([0,-4,0])
    cylinder(d=3.2,h=20,center=true,$fn=12);
}

difference()
{
translate([0,-4.5,-4.5])cylinder(d=10,h=2,$fn=30);
translate([0,-4.5,-4.5])cylinder(d=2.8,h=2,$fn=12);
}
}
}

module upper_plate(){
difference(){
union(){
cylinder(d=120,h=3);
translate([-26.5,55,0])rotate([0,0,-90]){
translate([13.97,2.5,0])cylinder(d=8,h=6);
translate([15.24,50.7,0])cylinder(d=8,h=6);
translate([66.04,7.6,0])cylinder(d=8,h=6);
translate([66.04,35.5,0])cylinder(d=8,h=6);
}
}

translate([39,-27.5,-1])cube(55);
scale([-1,1,1])translate([39,-27.5,-1])cube(55);
translate([44,34,-1])cylinder(d=3.2,h=5);    
translate([-44,34,-1])cylinder(d=3.2,h=5);    
translate([44,-34,-1])cylinder(d=3.2,h=5);    
translate([-44,-34,-1])cylinder(d=3.2,h=5);
translate([0,-25,-1])cylinder(d=20,h=5);
translate([0,-42,-1])cylinder(d=3.2,h=5);
rotate([0,0,35])translate([0,-42,-1])cylinder(d=3.2,h=5);    
rotate([0,0,-35])translate([0,-42,-1])cylinder(d=3.2,h=5);  

translate([-26.5,55,0])rotate([0,0,-90]){
translate([13.97,2.5,0])cylinder(d=2.9,h=10);
translate([15.24,50.7,0])cylinder(d=2.9,h=10);
translate([14.24,46.2,5])cube(6);
translate([66.04,7.6,0])cylinder(d=2.9,h=10);
translate([66.04,35.5,0])cylinder(d=2.9,h=10);
}
}
}

module motor_support(){
$fn=30;

difference(){
translate([-20.5,6,0])cube([41,20,22.35]);
translate([-12.5,15,-10])cube([25,12,50]);
translate([0,19.1,2.465])rotate([0,90,0])
cylinder(d=2.8,h=50,center=true,$fn=30);
translate([0,19.1,19.885])rotate([0,90,0])
cylinder(d=2.8,h=50,center=true,$fn=30);
translate([15,12,0])cylinder(d=2.8,h=30);    
translate([-15,12,0])cylinder(d=2.8,h=30);    
}
}

module motorandwheel(){
    difference(){
        union(){
        cube([18.7,37,22.3]);
        intersection(){
        translate([9.35,37,11.15])
        rotate([-90,0,0])cylinder(d=22.3,h=27.5);
        cube([18.7,65,22.3]);
        }
    }    
        translate([0,30.3,2.4])rotate([0,90,0])
        cylinder(d=3,h=20);
        translate([0,30.3,19.9])rotate([0,90,0])
        cylinder(d=3,h=20);
    }
    translate([35.7,11.2,11.15])rotate([0,-90,0])
    wheel();
}

module wheel(){
$fn=120;
difference(){
union(){
cylinder(h=2.5,d1=45,d2=50);
translate([0,0,2.5])cylinder(d=50,h=10);
translate([0,0,12.5])cylinder(h=2.5,d2=45,d1=50);
}
translate([0,0,7.5])
rotate_extrude(angle = 360, convexity = 2) {
translate([25.5,0,0])circle(1.6);
}
translate([0,0,3])cylinder(d=42,h=15);

for (i=[0:72:350]){
rotate([0,0,i])
translate([13,0,-1])cylinder(d=12,h=15,$fn=5);
}
}
difference(){
translate([0,0,0.001])cylinder(d=11,h=17.5);
translate([0,0,9.05])
scale(1.05)    // ajustar según impresora
    intersection(){
cylinder(d=5.35,h=9);
translate([0,0,4])cube([3.7,6,9],center=true);
    }
}
}

module pillar(){
    $fn=30;
difference(){
cylinder(d=7,h=32);
cylinder(d=2.8,h=10);
translate([0,0,22])cylinder(d=2.8,h=10);
}
}

module us_support(){
difference()
{
minkowski($fn=30){
cube([45.5,20,6],center=true);
cylinder(d=4,h=0.000001);
}
translate([0,0,2])cube([45.6,25,5],center=true);
    
translate([13,0,-5])cylinder(d=17,h=5,$fn=60);
translate([-13,0,-5])cylinder(d=17,h=5,$fn=60);
hull(){
translate([-3.5,7.5,-5])cylinder(d=4,h=5,$fn=60);
translate([3.5,7.5,-5])cylinder(d=4,h=5,$fn=60);
}
hull(){
translate([-3.5,-8,-5])cylinder(d=4,h=5,$fn=60);
translate([3.5,-8,-5])cylinder(d=4,h=5,$fn=60);
}
}
hull(){
translate([23,9,1.9])sphere(0.8,$fn=20);
translate([23,-9,1.9])sphere(0.8,$fn=20);
}
hull(){
translate([-23,9,1.9])sphere(0.8,$fn=20);
translate([-23,-9,1.9])sphere(0.8,$fn=20);
}
translate([9.5,14,-2.5])rotate([0,0,180])acuerdo();
translate([-9.5,14,-2.5])rotate([0,0,-90])acuerdo();

translate([-7.5,12,-3])cube([15,7,2.5]);
difference(){
translate([-7.5,17,-3])cube([15,2.5,11]);
translate([0,0,4])rotate([-90,0,0])
cylinder(d=3.2,h=20,$fn=30);
}
translate([-7.5,15,1.5])scale([7.5,1,1])
rotate([0,90,0])acuerdo();

module acuerdo(){
difference(){
cube(2);
cylinder(d=4,h=2,$fn=30);
}
}
}

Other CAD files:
3d_models/scad/lower_plate.scad
3d_models/scad/US_mount.scad
3d_models/scad/US_support.scad
3d_models/scad/pillar.scad
3d_models/scad/upper_plate.scad

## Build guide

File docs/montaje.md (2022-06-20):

# Montaje Sapoconcho

Ahora que ya tienes tu kit, ¡vamos a montar el Sapoconcho!

## Montaje mecánico
El chasis base tiene pocas piezas y el montaje es muy sencillo.

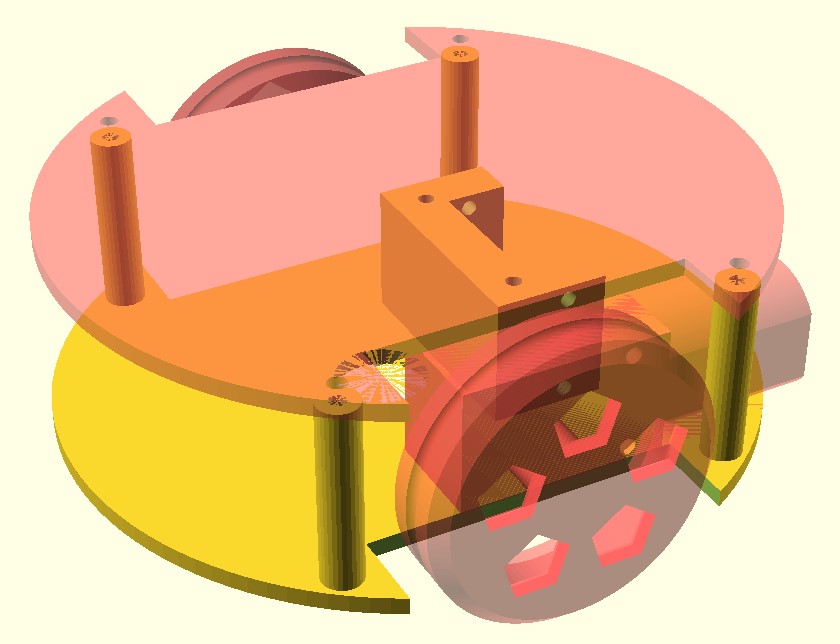
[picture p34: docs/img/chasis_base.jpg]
Chasis base


**Paso 1**: Los motores amarillos se unirán al soporte con 4 tornillos M3x30.

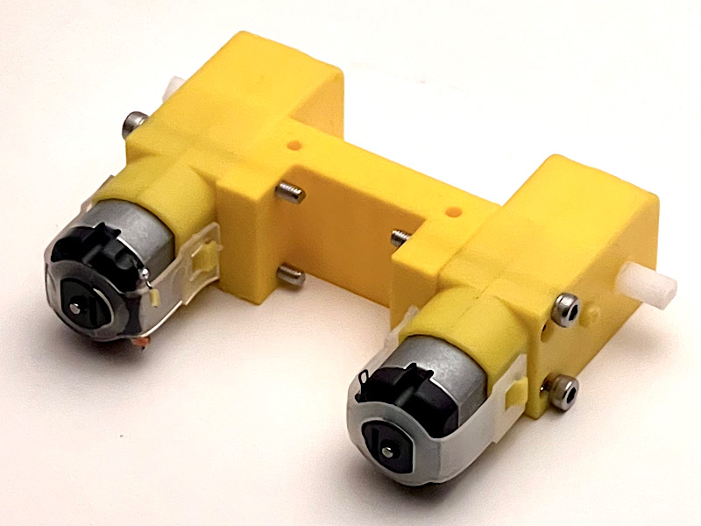
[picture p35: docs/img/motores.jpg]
Motores


**Paso 2**: Unir la base inferior al soporte con dos tornillos M3x12. También se puede poner ahora la bola loca o 'ballcaster', el tercer punto de apoyo.

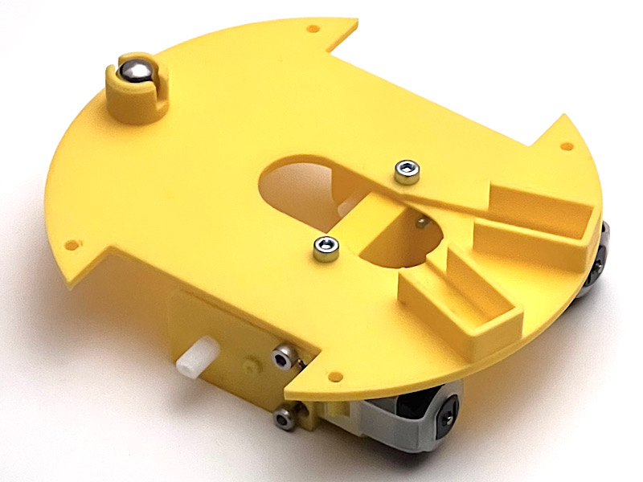
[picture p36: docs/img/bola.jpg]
Bola


**Paso 3**: Montar los 4 pilares a la base inferior con 4 tornillos M3x10.

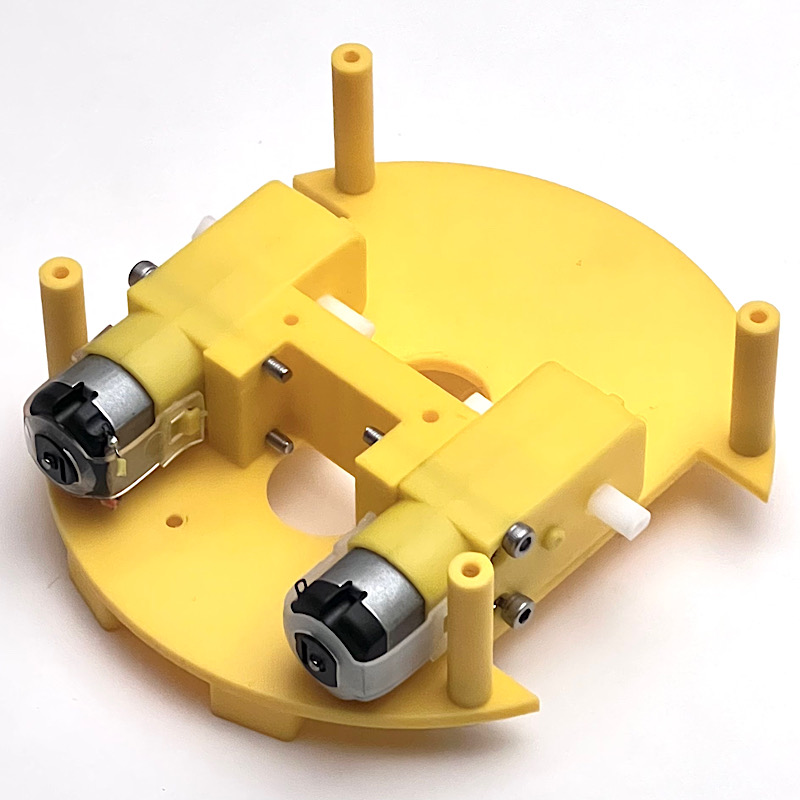
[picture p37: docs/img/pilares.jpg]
Pilares


**Paso 4**: Montar la base superior a los pilares con otros 4 tornillos M3x10. Ojo a la orientación en la foto.

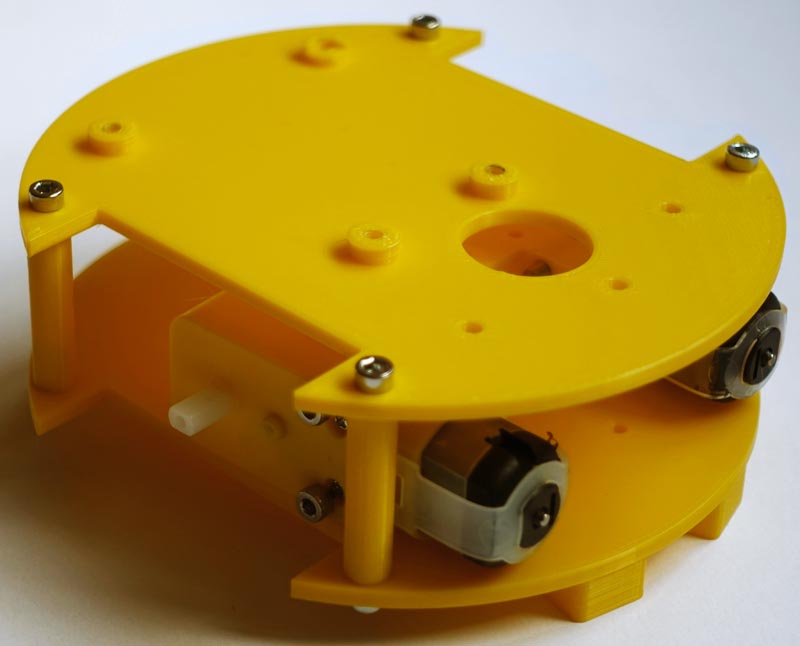
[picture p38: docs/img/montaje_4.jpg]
Base superior


**Paso 5**: Colocar las ruedas -cada una con su 'neumático'-, montar el Arduino UNO con tornillos M3 (dos en diagonal son suficientes) y pinchar la Shield sobre él.

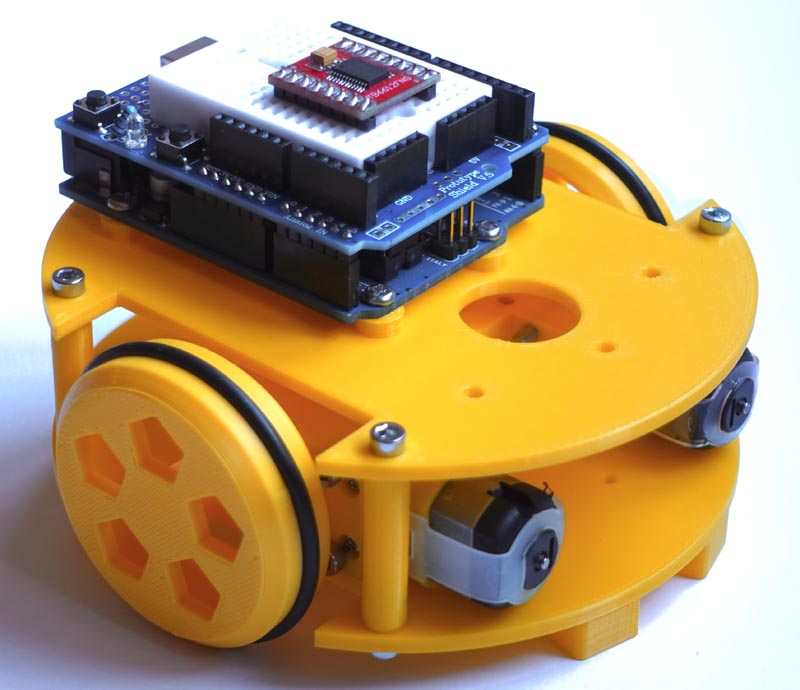
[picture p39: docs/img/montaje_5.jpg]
Ruedas


## Montaje eléctrico
Arduino no puede operar directamente un motor. Necesita un intermediario o driver. En este caso utilizaremos el DRV8833.

!!! Note "Nota"

    Con una pequeña variación en el cableado, el driver Toshiba TB6612 también es compatible.

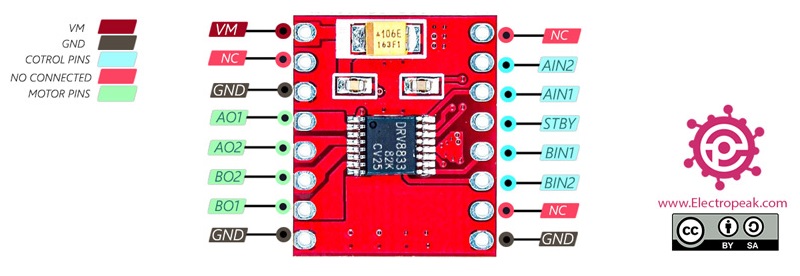
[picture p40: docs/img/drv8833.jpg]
drv8833


Para conectar el driver vamos a usar cable rígido de colores cortado a medida. Las conexiones son las de la imagen. Aunque el color de los cables no influye en el funcionamiento, para la alimentación y masa (tierra) se suelen utilizar los colores rojo y negro respectivamente.

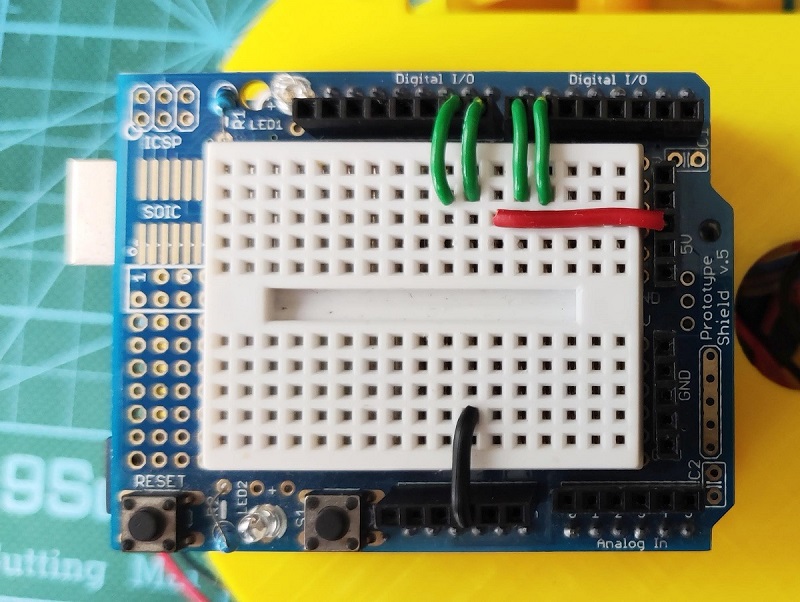
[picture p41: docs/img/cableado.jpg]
cableado


A continuación hay que pinchar el driver teniendo cuidado con que los pines y los cable coincidan como en la foto.

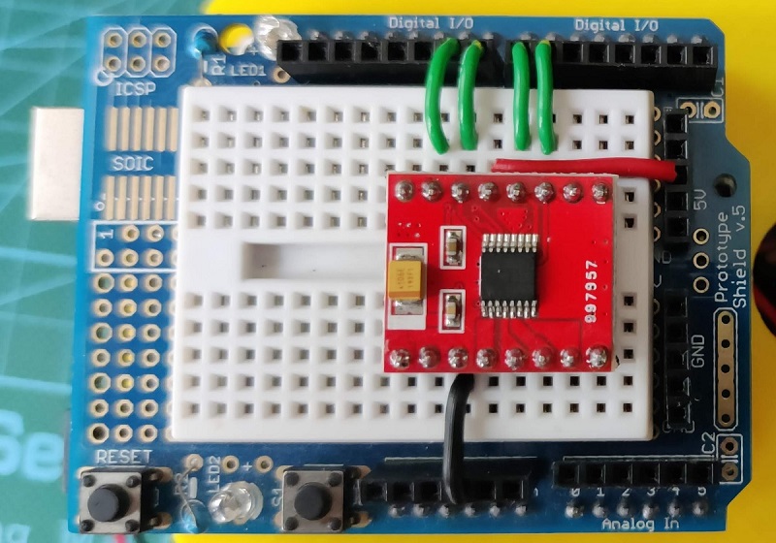
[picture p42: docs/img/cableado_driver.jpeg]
cableado driver


**Cableado de los motores**  
Necesitamos cuatro cables Dupont de 20cmm soldados en un extremos a los motores y con punta macho en el otro extremo para la protoshield. Pueden ir agrupados para hacer un montaje más elegante, aunque no es imprescindible. Tampoco es imprescindible, pero si una buena idea añadir un condensador cerámico de 0.1uF (código 104) en paralelo en cada motor.

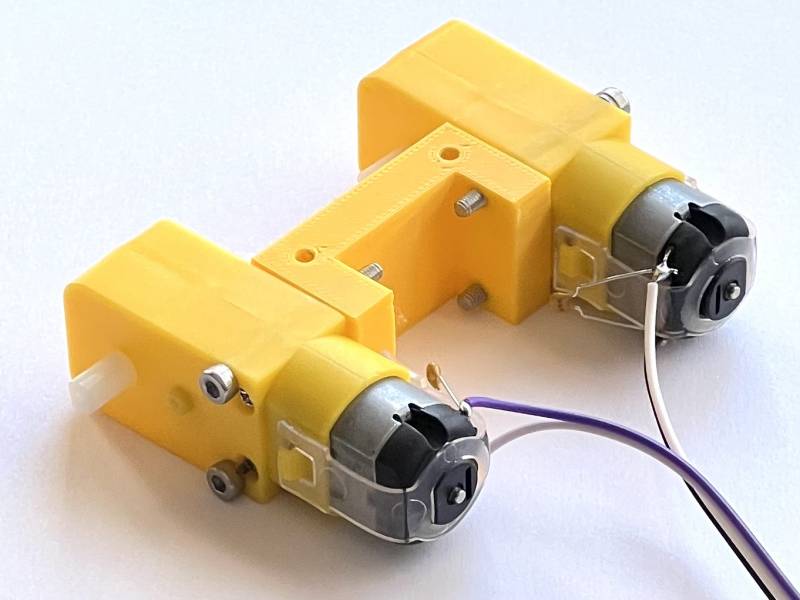
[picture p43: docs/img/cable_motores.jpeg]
cable motores


Los cables Dupont que vengan de los motores se conectarán ahora en los pines correspondientes.

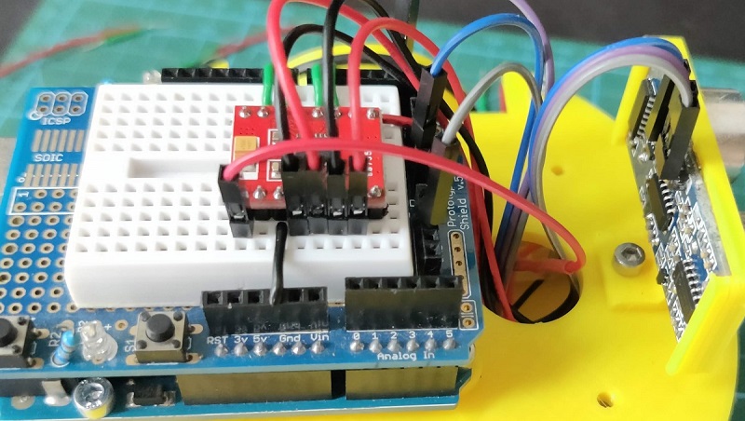
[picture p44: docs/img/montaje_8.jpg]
Pines motores


Si al probar las funciones de movimiento alguna rueda gira al revés, puedes intercambiar los cables de ese motor.

**Alimentación**  
Para alimentación utilizaremos un portapilas para 4 pilas AA. Y para que valga para cualquier proyecto, puedas usar pilas recargables y reduzcamos la contaminación añadiremos siempre un regulador dc-dc elevador para elevar la tensión de salida (step-up). El LM2587 y el XL6009 valen y tienen un tornillo para regular la tensión de salida; un buen valor es 7,5v.

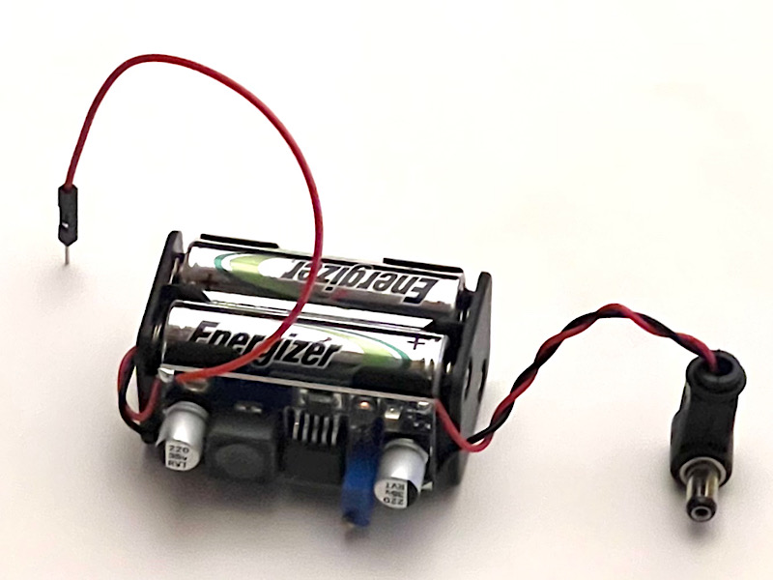
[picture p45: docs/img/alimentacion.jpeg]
Alimentacion


Las conexiones del step-up son muy sencillas: entrada positiva/negativa (IN+ rojo/IN- negro) desde el portapilas y salida positiva/negaviva (OUT+ rojo/OUT- negro) a la clavija. Además sacaremos un cable con un extremo Dupont macho (bstante largo) para alimentar el driver antes del step-up, de IN+ a VM.

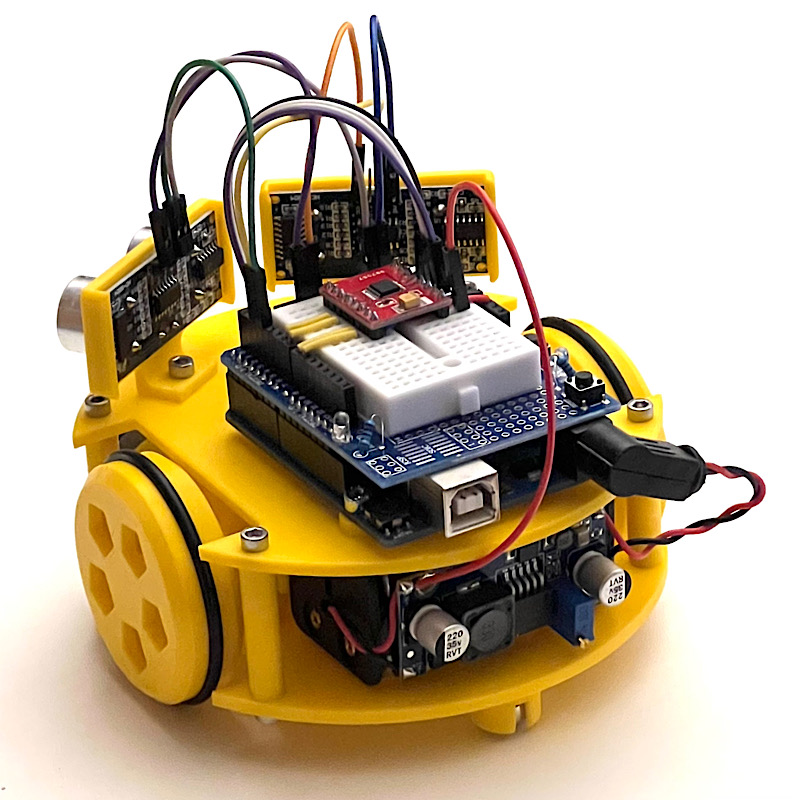
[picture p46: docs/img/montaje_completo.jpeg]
Montaje completo


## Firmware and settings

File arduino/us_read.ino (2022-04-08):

// Configuración
void setup()
{
  Serial.begin(9600);
}

// Programa común
void loop()
{
  unsigned long distancia = sonar(2);    // invocamos a función de medir distancia
  Serial.print("Distancia: ");  // imprimimos los valores en la consola
  Serial.print(distancia);
  Serial.println(" mm");
}

// Función
unsigned long sonar(int trig)
{
  pinMode(trig, OUTPUT);
  digitalWrite(trig,LOW); // trigger envia un pulso ultrasónico
  delayMicroseconds(5);
  digitalWrite(trig, HIGH);     
  delayMicroseconds(10);
  pinMode(trig, INPUT);
  unsigned long tiempo=pulseIn(trig, HIGH);    // echo espera a recibir la respuesta
  unsigned long distancia= int(0.17*tiempo);  // fórmula para calcular la distancia
  return distancia;
}

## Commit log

2022-05-03 Added usb wire and solder uc pins
2022-05-03 Changed to mkdocs material
2022-05-20 arduino quickstart
